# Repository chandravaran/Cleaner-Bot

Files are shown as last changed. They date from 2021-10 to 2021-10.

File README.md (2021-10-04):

# Cleaner-Bot

This repository contains the CAD models, DXF files used for laser cutting, followed by the code used to control the robot. The projects aim was to design and implement a new design as an alternative to the currently existing cleaner robots. 

For prezi presentation click [here](https://prezi.com/view/AhR2JavvCEbZ34JITC9l/)
Youtube video [Link](https://youtu.be/4qz2bjRoqZo)

## Table of Contents
1. [Design Phases](#Design-Phases)
2. [Simulation](#simulation)
3. [Laser Cutting Images](#laser-cut-images)
4. [Assembly](#assembly)
5. [Robot Control](#robot-control)

## Design Phases
This section we will discuss about the different stages the robot design process went through.

### Design 1
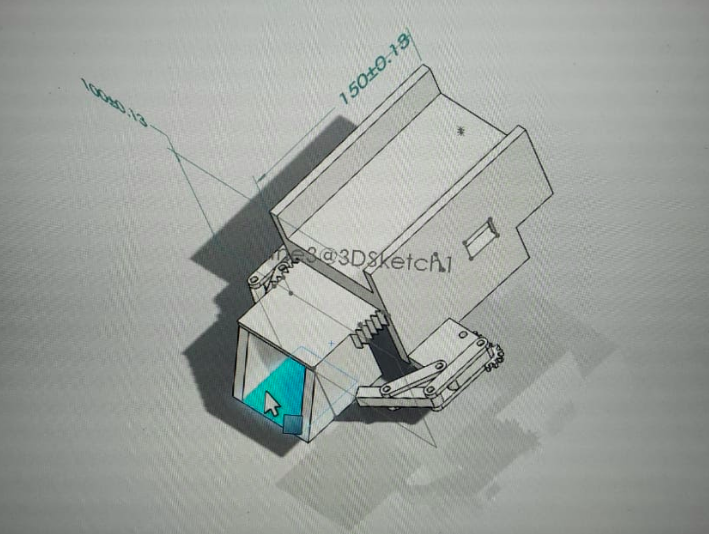
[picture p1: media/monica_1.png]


The above picture is the initial design for the cleaner robot. It accomplished our objective of making the setup small. Still, there exited a problem as very little space is available to keep electronic components. Also, no vacuum chamber that would collect the fine dust, which currently commercialized robots already do. For these reasons, we started designing the next model.

### Design 2 
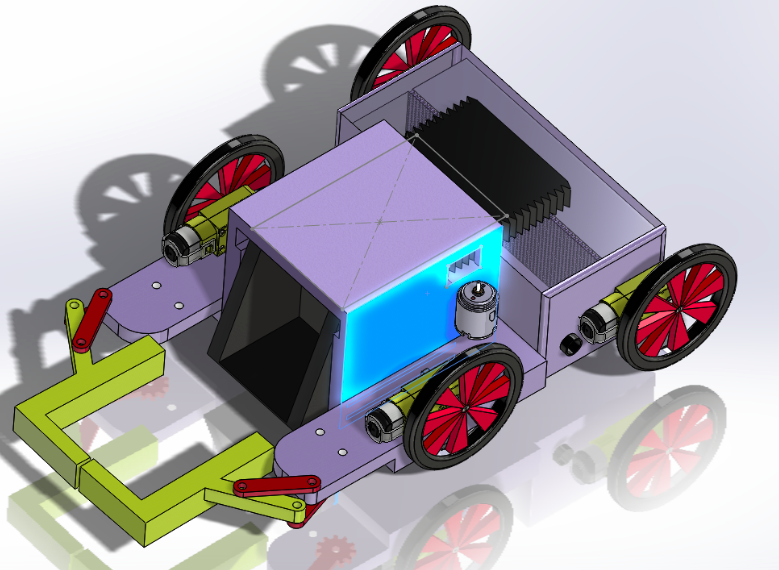
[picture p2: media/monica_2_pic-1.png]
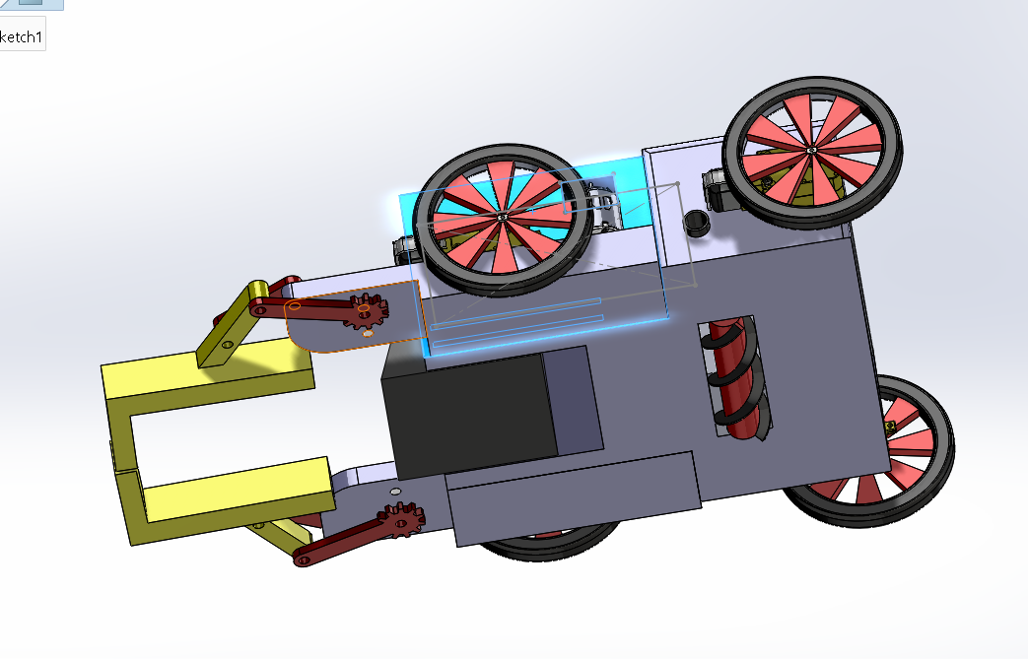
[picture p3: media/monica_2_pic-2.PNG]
  

Keeping in mind the drawbacks of the previous model, we added a vacuum chamber, and the electronics were moved from the front to the back. But there was a considerable drawback of this design, including the electronics at the back made the robot long, which includes the arms in closed form. Also, we concluded that the linearly actuated front bin was taking up too much space and would be very hard to manufacture, as 3D-printed gears would have difficulty meshing if not made properly. Thus the final design came into existence.

### Design 3 
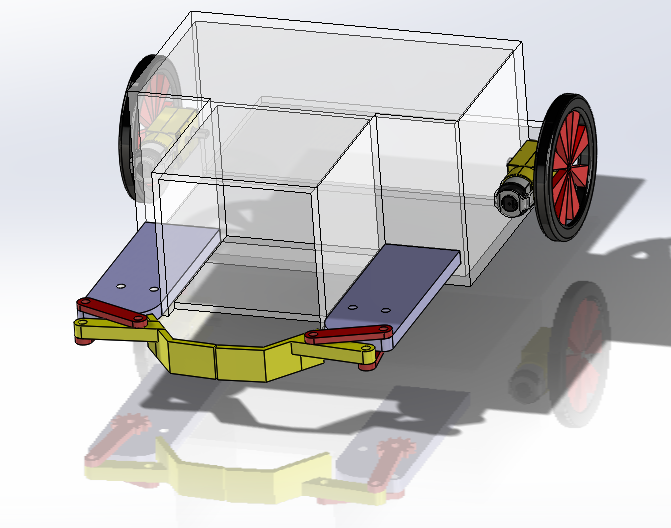
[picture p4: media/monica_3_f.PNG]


The above picture represents a minimalistic design. It includes all the main components we wanted. The front bin was removed, and a flap-like structure was made. The arms were changed so they could come as close to the body as possible. This design was finalized for manufacturing.

## Simulation
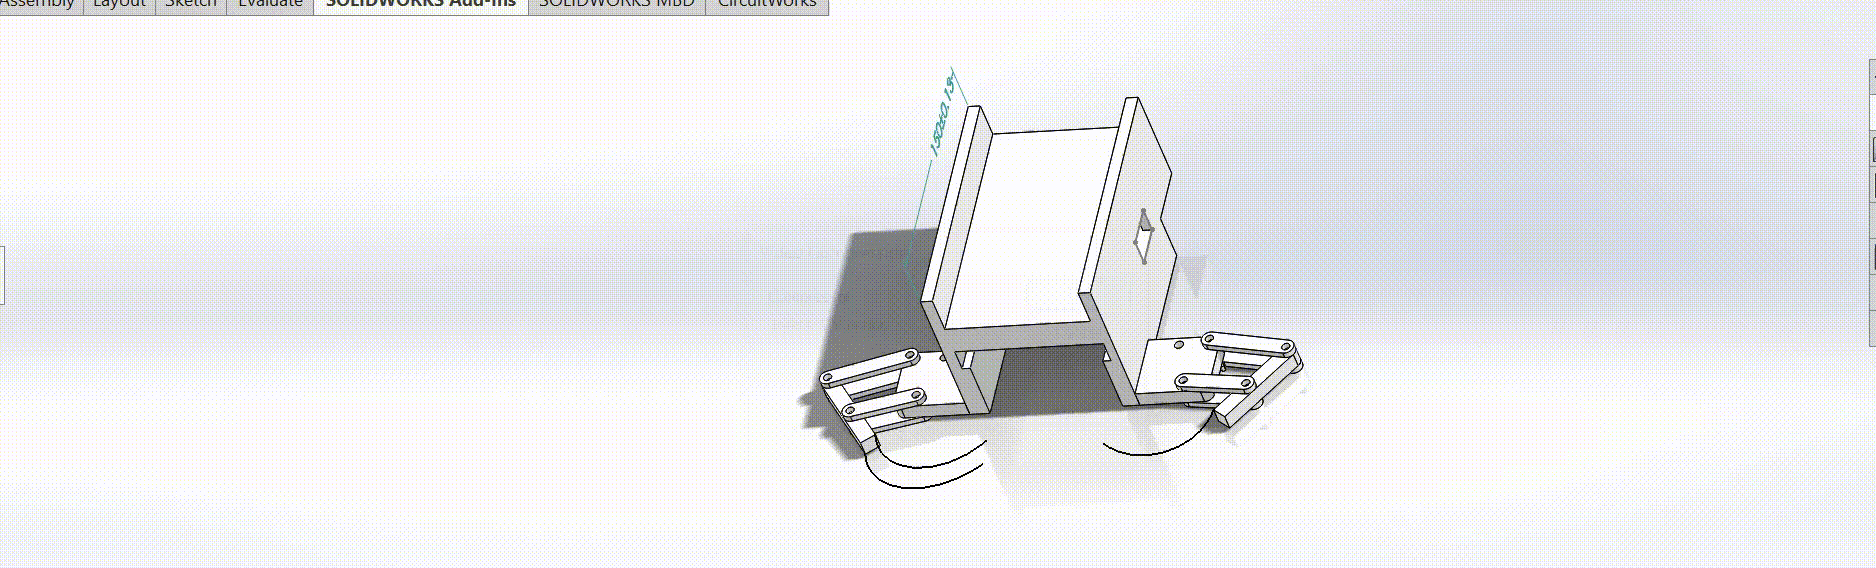
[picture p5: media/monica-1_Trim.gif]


The above is a small simulation of the arm trajectories used to pick the 4 bar mechanisms configuration. The same configuration was used for all the designs.

## Laser Cutting Images
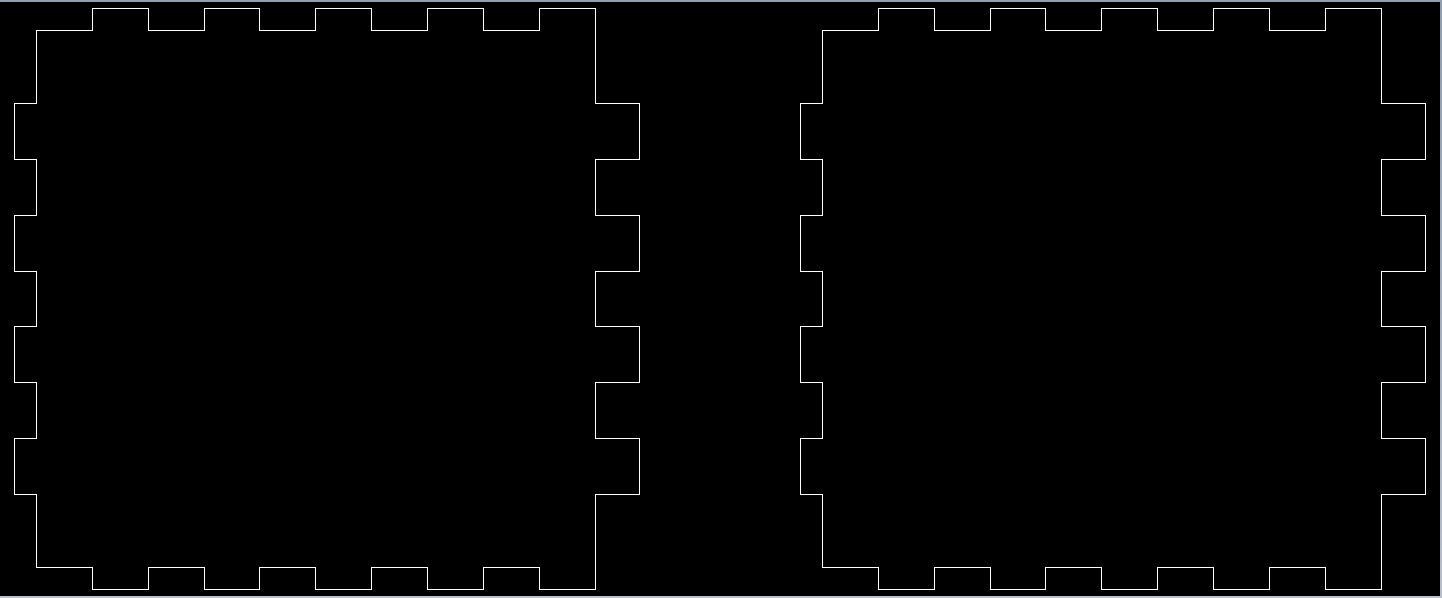
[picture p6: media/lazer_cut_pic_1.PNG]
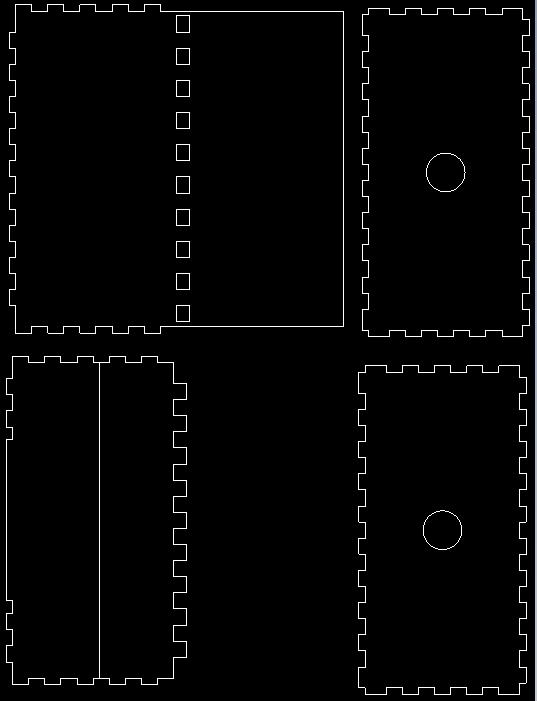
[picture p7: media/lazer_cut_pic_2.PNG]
  

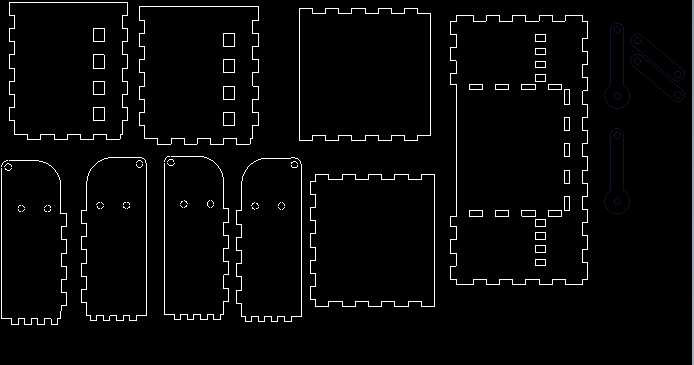
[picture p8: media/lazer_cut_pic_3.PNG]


The above images are the screenshots from the DXF files used as inputs into the laser cutter. The 3D assembly was converted into various 2D parts, and the teeth were added to these 2D projections.

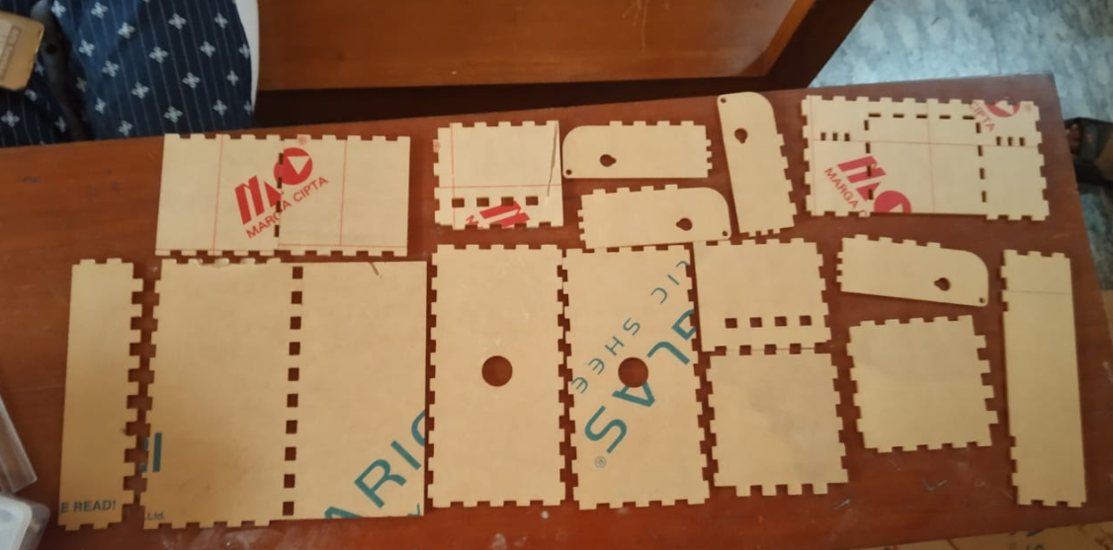
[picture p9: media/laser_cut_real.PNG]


After acquiring the required material, the acrylic was laser cut, as shown above.

## Assembly 
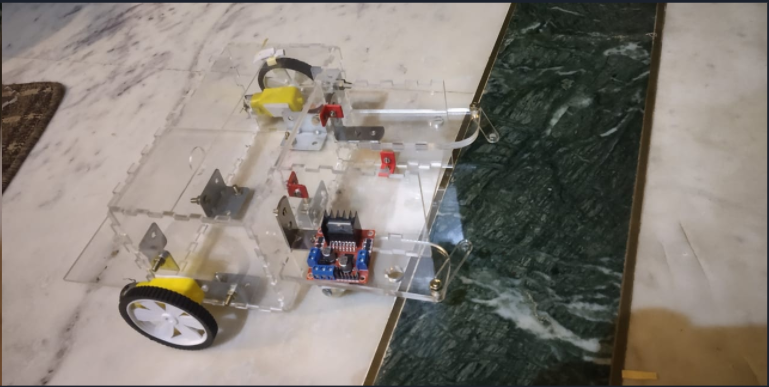
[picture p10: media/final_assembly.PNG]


The above image is the assembly of the laser cut parts. Various types of L clamps were used for assembly.

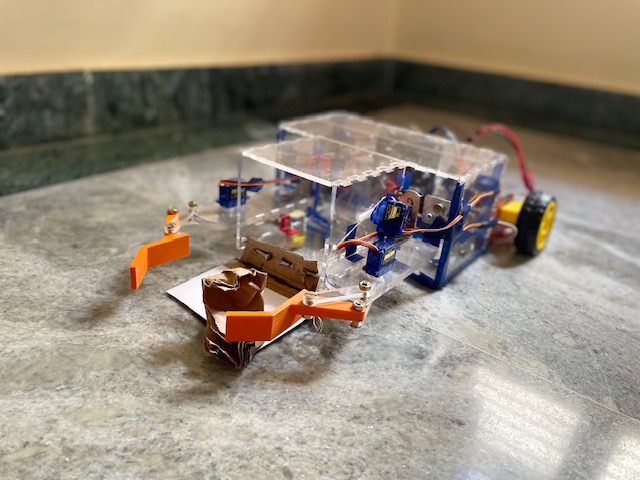
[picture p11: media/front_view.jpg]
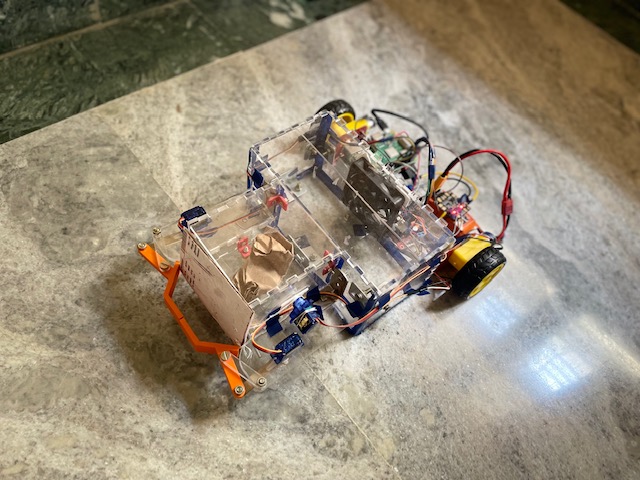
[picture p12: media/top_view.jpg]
 

These 2 images are the front and top view of the final robot with electronics. After the final assembly, we realized that wiring should also be considered when the next model is made. The front arms were 3D printed, and the flap was made using cardboard as the servo we are using has a low torque rating, so the flap should be light.

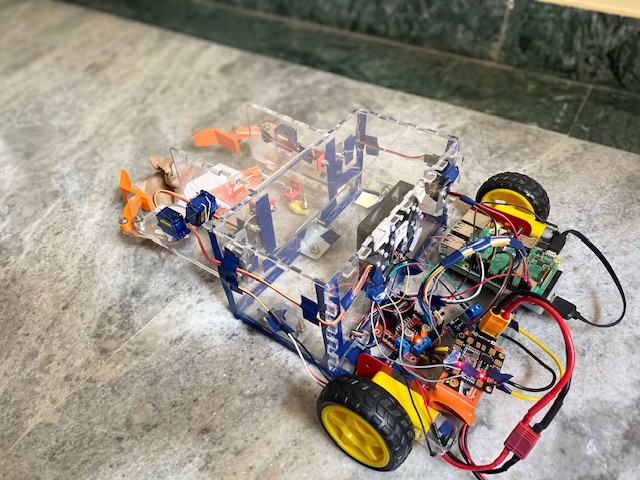
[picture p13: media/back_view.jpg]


This is the back picture of the robot. There is a motor driver, a Lipo, RPi, and a trigger switch. We initially thought of using an Arduino nano, but there were not enough pins, and the RPi allows us to control the robot using SSH.   

## Robot Control

This code allows us teleoperation control of cleaner bot.
The input is a keyboard press, with the following options

Moving around:<br/>
<p>u &emsp; i &emsp; o</p>
<p>j &emsp; k &emsp; l</p>
<p>m &emsp; , &emsp; .</p>

1 : Low <br/>
2 : Medium<br/>
3 : High<br/>

c: Closing the front arms<br/>
v: Opening the front arms<br/>

d: Closing the front flap<br/>
f: opening the front flap<br/>

r: Fan on<br/>
t: Fan on<br/>

e: to quit<br/>

This is printed in the terminal so we don't have to remember the commands.

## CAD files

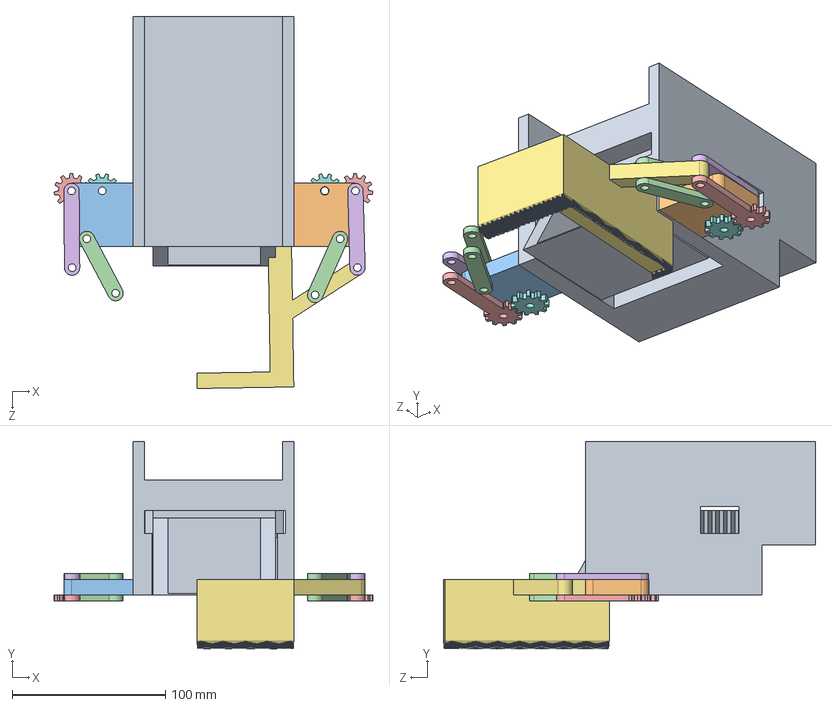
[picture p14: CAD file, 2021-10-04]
Cleaner_bot_1.SLDASM
207.7 x 135.0 x 242.4 mm
four_bar2-L
four_bar2-R
four_bar1 x 4
four_bar_gear x 2
four_bar4 x 2
four_bar3
gear_servo x 2
bucket

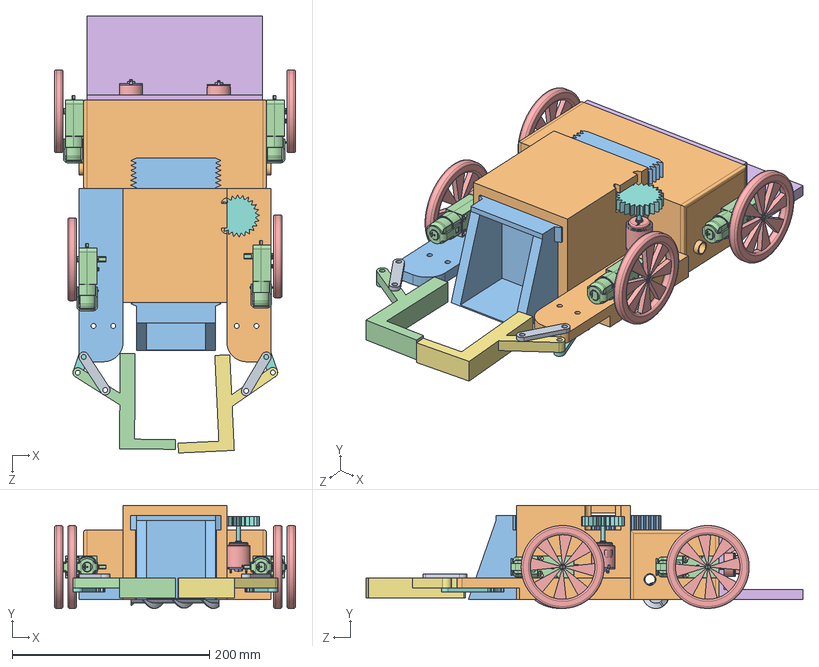
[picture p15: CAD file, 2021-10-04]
Cleaner_bot_2.SLDASM
244.6 x 104.4 x 442.7 mm
roller
bucket
DC Geared Motor x 4
Motor Casing x 3
Motor Cap x 3
Motor Maginet x 6
Motor Bearing x 3
Magnet Spring x 3
Motor Shaft x 3
Stamped Plate x 57
Stamped Plate Cover x 6
Shaft Bearing x 3
Contact Mount x 3
Contact x 9
Contact Retainer x 3
Insulator Cap x 3
Insulator Cap 2 x 3
Copper windings x 9
Cap Bearing x 3
Brush^Motor x 6
Wiring Post x 6
four_bar3
four_bar_gear x 2
four_bar1 x 2
four_bar2-L
four_bar2-R
four_bar3_R
back_section
fan x 2
gear

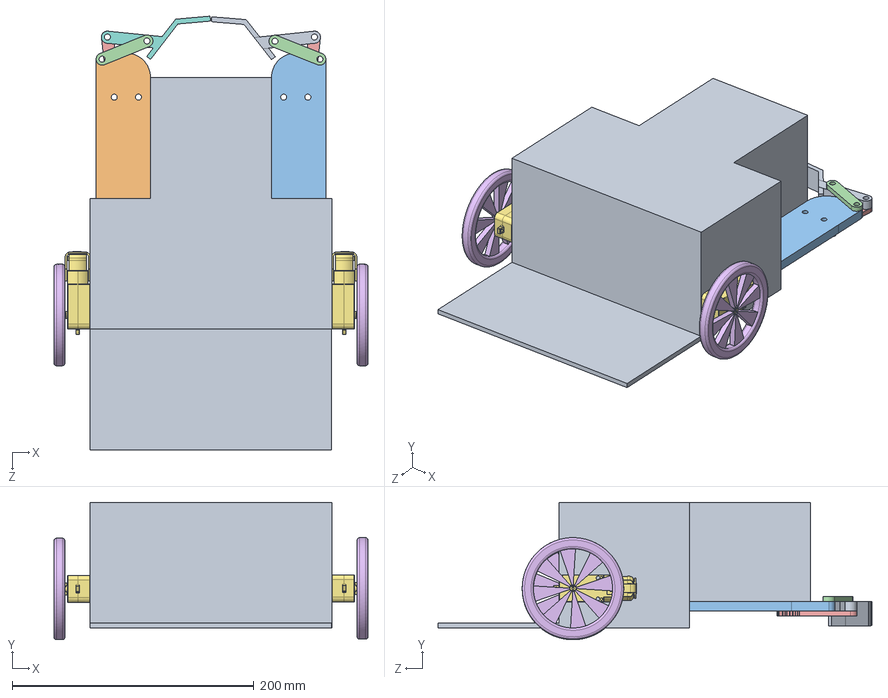
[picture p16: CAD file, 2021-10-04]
Cleaner_bot_final.SLDASM
259.6 x 113.7 x 358.6 mm
monica_3_body1
monica_3_left_side
monica_3_right_side
four_bar1 x 2
four_bar_gear x 2
DC Geared Motor x 2
monica_3_arm_left
monica_3_arm_right

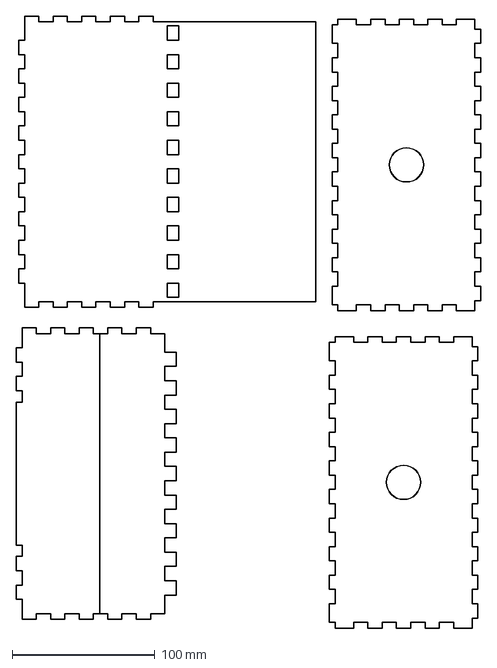
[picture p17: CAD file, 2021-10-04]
monica_lazer_cutting_back_box.DXF
325.1 x 428.4 mm

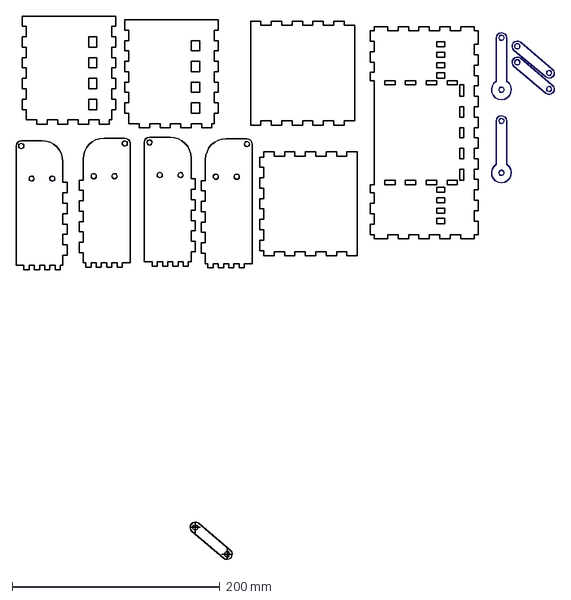
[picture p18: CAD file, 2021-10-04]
monica_3_front_lazer_cut2.DXF
518.6 x 523.6 mm

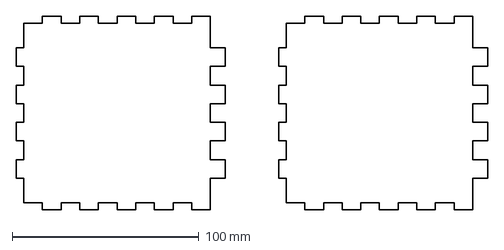
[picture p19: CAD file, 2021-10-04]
monica_lazer_cutting_side.DXF
252.7 x 104.0 mm

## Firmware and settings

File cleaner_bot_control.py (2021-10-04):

'''
Name: cleaner_bot_controller.py
Author: Chandravaran Kunjeti
'''

import time
import RPi.GPIO as GPIO
import sys, select, termios, tty

'''
Class that contains all the function required to control the robot.
'''
class CleanerBotControl:
    def __init__(self):
        '''
        Looking at the robot from the back the naming convention is given.
        '''
        self.motor_left_in1  = 24  # Pin for the left motor positive terminal
        self.motor_left_in2  = 23  # Pin for the left motor negative terminal
        self.motor_left_en   = 25  # Pin to enable the left motor
        self.motor_right_in1 = 4   # Pin for the right motor positive terminal
        self.motor_right_in2 = 27  # Pin for the right motor negative terminal
        self.motor_right_en  = 22  # Pin to enable the right motor

        self.servo1_left_pin  = 19 # PWM pin of the left front motor-servo
        self.servo2_right_pin = 26 # PWM pin of the right front motor-servo
        self.servo3_flap_pin  = 21 # PWM pin of the flap motor-servo

        self.fan_motor_pin = 12 # Trigger pin for the PC Fan.

        self.count = 1 # Varriable to reprint the options.

        # Setting Mode
        GPIO.setmode(GPIO.BCM)

        # Setup
        GPIO.setup(self.motor_right_in1,GPIO.OUT)
        GPIO.setup(self.motor_right_in2,GPIO.OUT)
        GPIO.setup(self.motor_right_en,GPIO.OUT)

        GPIO.setup(self.motor_left_in1,GPIO.OUT)
        GPIO.setup(self.motor_left_in2,GPIO.OUT)
        GPIO.setup(self.motor_left_en,GPIO.OUT)

        GPIO.setup(self.servo1_left_pin,GPIO.OUT)
        GPIO.setup(self.servo2_right_pin,GPIO.OUT)
        GPIO.setup(self.servo3_flap_pin,GPIO.OUT)

        GPIO.setup(self.fan_motor_pin,GPIO.OUT)

        # Initialization
        GPIO.output(self.motor_right_in1,GPIO.LOW)
        GPIO.output(self.motor_right_in2,GPIO.LOW)

        GPIO.output(self.motor_left_in1,GPIO.LOW)
        GPIO.output(self.motor_left_in2,GPIO.LOW)

        GPIO.output(self.fan_motor_pin,GPIO.LOW)

        # Setting up pdm on enable pin
        self.motor_right=GPIO.PWM(self.motor_right_en,1000)
        self.motor_left=GPIO.PWM(self.motor_left_en,1000)

        self.servo1 = GPIO.PWM(self.servo1_left_pin,50)
        self.servo2 = GPIO.PWM(self.servo2_right_pin,50)
        self.servo3 = GPIO.PWM(self.servo3_flap_pin,50)

        self.duty_cycle_right = 40
        self.duty_cycle_left  = 40

        # Keeping low speed
        self.motor_right.start(self.duty_cycle_right)
        self.motor_left.start(self.duty_cycle_left)
        self.servo1.start(0)
        self.servo2.start(0)
        self.servo3.start(0)

        self.msg = """

        This code allows us teleoperation control of cleaner bot.

        The input is a keyboard press, with the following options

        ---------------------------
        Moving around:
        u    i    o
        j    k    l
        m    ,    .
        anything else : stop
        1 : Low
        2 : Medium
        3 : High

        c: Closing the front arms
        v: Opening the front arms

        d: Closing the front flap
        f: opening the front flap

        r: Fan on
        t: Fan on

        e: to quit
        ---------------------------
        """

        print(self.msg)

        self.main()

    '''
    Brief: The Function to move forward.
    '''
    def moveForward(self):
        # Right Motor
        GPIO.output(self.motor_right_in1,GPIO.HIGH)
        GPIO.output(self.motor_right_in2,GPIO.LOW)

        # Left Motor
        GPIO.output(self.motor_left_in1,GPIO.HIGH)
        GPIO.output(self.motor_left_in2,GPIO.LOW)

        print("Forward")

    '''
    Brief: The Function to stop the robot.
    '''
    def stop(self):
        # Right Motor
        GPIO.output(self.motor_right_in1,GPIO.LOW)
        GPIO.output(self.motor_right_in2,GPIO.LOW)

        # Left Motor
        GPIO.output(self.motor_left_in1,GPIO.LOW)
        GPIO.output(self.motor_left_in2,GPIO.LOW)

        print("Stop")

    '''
    Brief: The Function to move backward.
    '''
    def moveBackward(self):
        # Right Motor
        GPIO.output(self.motor_right_in1,GPIO.LOW)
        GPIO.output(self.motor_right_in2,GPIO.HIGH)

        # Left Motor
        GPIO.output(self.motor_left_in1,GPIO.LOW)
        GPIO.output(self.motor_left_in2,GPIO.HIGH)
        print("Backward")

    '''
    Brief: The Function to turn left in place.
    '''
    def turnLeftInPlace(self):

        # Right Motor
        GPIO.output(self.motor_right_in1,GPIO.HIGH)
        GPIO.output(self.motor_right_in2,GPIO.LOW)

        # Left Motor
        GPIO.output(self.motor_left_in1,GPIO.LOW)
        GPIO.output(self.motor_left_in2,GPIO.HIGH)
        print("Turn left in place")

    '''
    Brief: The Function to turn right in place.
    '''
    def turnRightInPlace(self):

        # Right Motor
        GPIO.output(self.motor_right_in1,GPIO.LOW)
        GPIO.output(self.motor_right_in2,GPIO.HIGH)

        # Left Motor
        GPIO.output(self.motor_left_in1,GPIO.HIGH)
        GPIO.output(self.motor_left_in2,GPIO.LOW)
        print("Turn right in place")

    '''
    Brief: The Function to turn left about left wheel while moving forward.
    '''
    def turnLeftAboutLeftWheelFront(self):
        # Right Motor
        GPIO.output(self.motor_right_in1,GPIO.HIGH)
        GPIO.output(self.motor_right_in2,GPIO.LOW)

        # Left Motor
        GPIO.output(self.motor_left_in1,GPIO.LOW)
        GPIO.output(self.motor_left_in2,GPIO.LOW)
        print("Turn left about left wheel front")

    '''
    Brief: The Function to turn right about right wheel while moving forward.
    '''
    def turnRightAboutRightWheelFront(self):
        # Right Motor
        GPIO.output(self.motor_right_in1,GPIO.LOW)
        GPIO.output(self.motor_right_in2,GPIO.LOW)

        # Left Motor
        GPIO.output(self.motor_left_in1,GPIO.HIGH)
        GPIO.output(self.motor_left_in2,GPIO.LOW)
        print("Turn right about right wheel front")

    '''
    Brief: The Function to turn left about left wheel while moving backward.
    '''
    def turnLeftAboutLeftWheelBack(self):
        # Right Motor
        GPIO.output(self.motor_right_in1,GPIO.LOW)
        GPIO.output(self.motor_right_in2,GPIO.HIGH)

        # Left Motor
        GPIO.output(self.motor_left_in1,GPIO.LOW)
        GPIO.output(self.motor_left_in2,GPIO.LOW)
        print("Turn left about left wheel back")

    '''
    Brief: The Function to turn right about right wheel while moving backward.
    '''
    def turnRightAboutRightWheelBack(self):
        # Right Motor
        GPIO.output(self.motor_right_in1,GPIO.LOW)
        GPIO.output(self.motor_right_in2,GPIO.LOW)

        # Left Motor
        GPIO.output(self.motor_left_in1,GPIO.LOW)
        GPIO.output(self.motor_left_in2,GPIO.HIGH)

        print("Turn right about right wheel back")

    '''
    Brief: The Function to close the front arms, as the servo in use is a 360* servo
    so it uses velocities to move. As there is no proper relation for between the speed
    of revolution and direction. I am commanding one servo to move for a longer period of
    time.
    '''
    def closeFront(self):
        self.servo1.ChangeDutyCycle(11)
        self.servo2.ChangeDutyCycle(6)
        time.sleep(0.25)
        self.servo1.ChangeDutyCycle(1)
        time.sleep(0.2)
        self.servo2.ChangeDutyCycle(1)

    '''
    Brief: The Function to open the front arms, as the servo in use is a 360* servo
    so it uses velocities to move. As there is no proper relation for between the speed
    of revolution and direction. I am commanding one servo to move for a longer period of
    time.
    '''
    def openFront(self):
        self.servo1.ChangeDutyCycle(6)
        self.servo2.ChangeDutyCycle(11)
        time.sleep(0.25)
        self.servo2.ChangeDutyCycle(1)
        time.sleep(0.2)
        self.servo1.ChangeDutyCycle(1)

    '''
    Brief: The Function to close the front flap.
    '''
    def flapUp(self):
        self.servo3.ChangeDutyCycle(0.1)

    '''
    Brief: The Function to open the front flap.
    '''
    def flapDown(self):
        self.servo3.ChangeDutyCycle(11.9)

    '''
    Brief: The Function to switch on the vaccum fan.
    '''
    def fanOn(self):
        GPIO.output(self.fan_motor_pin,GPIO.HIGH)

    '''
    Brief: The Function to switch off the vaccum fan.
    '''
    def fanOff(self):
        GPIO.output(self.fan_motor_pin,GPIO.LOW)

    '''
    Brief: The Function to set the duty cycles for the back wheels, to control the speed.
    '''
    def setDuty(self,right,left):
        self.motor_right.ChangeDutyCycle(right)
        self.motor_left.ChangeDutyCycle(left)
        
    '''
    Brief: The function that takes the keyboard interupt
    '''
    def getKey(self):
        tty.setraw(sys.stdin.fileno())
        rlist, _, _ = select.select([sys.stdin], [], [], 0.1)
        if rlist:
            key = sys.stdin.read(1)
        else:
            key = ''
        termios.tcsetattr(sys.stdin, termios.TCSADRAIN,termios.tcgetattr(sys.stdin))
        return key

    '''
    Brief: The main function that takes in keyboard input.
    '''
    def main(self):
        while(1):
            key =self.getKey() #raw_input()

            try:
                if key=='k':
                    self.stop()
                    self.count += 1

                elif key=='i':
                    self.moveForward()
                    key='z'
                    self.count += 1

                elif key==',':
                    self.moveBackward()
                    key='z'
                    self.count += 1

                elif key=='j':
                    self.turnLeftInPlace()
                    key='z'

                elif key=='l':
                    self.turnRightInPlace()
                    key='z'
                    self.count += 1

                elif key=='u':
                    self.turnLeftAboutLeftWheelFront()
                    key='z'
                    self.count += 1

                elif key=='o':
                    self.turnRightAboutRightWheelFront()
                    key='z'
                    self.count += 1

                elif key=='m':
                    self.turnLeftAboutLeftWheelBack()
                    key='z'
                    self.count += 1

                elif key=='.':
                    self.turnRightAboutRightWheelBack()
                    key='z'
                    self.count += 1

                elif key=='1':
                    self.setDuty(40,40)
                    print("Low")
                    key='z'
                    self.count += 1

                elif key=='2':
                    self.setDuty(70,70)
                    print("Medium")
                    key='z'
                    self.count += 1

                elif key=='3':
                    self.setDuty(100,100)
                    print("High")
                    key='z'
                    self.count += 1

                elif key=='c':
                    self.closeFront()
                    self.count += 1
                    print("close")
                    key = 'z'

                elif key=='v':
                    self.openFront()
                    self.count += 1
                    print("open")
                    key = 'z'

                elif key=='f':
                    self.flapUp()
                    self.count += 1
                    print("Close Flap")
                    key = 'z'

                elif key=='d':
                   self.flapDown()
                   self.count += 1
                   print("Open Flap")
                   key = 'z'

                elif key=='r':
                    self.fanOn()
                    self.count += 1
                    print("Fan On")
                    key = 'z'

                elif key=='t':
                   self.fanOff()
                   self.count += 1
                   print("Fan off")
                   key = 'z'

                elif key=='e':
                    GPIO.cleanup()
                    print("GPIO Clean up")
                    break

                if self.count%10 == 0:
                    print(self.msg)

            except Exception as e:
                print(e)

            finally:
               termios.tcsetattr(sys.stdin, termios.TCSADRAIN,termios.tcgetattr(sys.stdin))



if __name__ == "__main__":
    control = CleanerBotControl()
